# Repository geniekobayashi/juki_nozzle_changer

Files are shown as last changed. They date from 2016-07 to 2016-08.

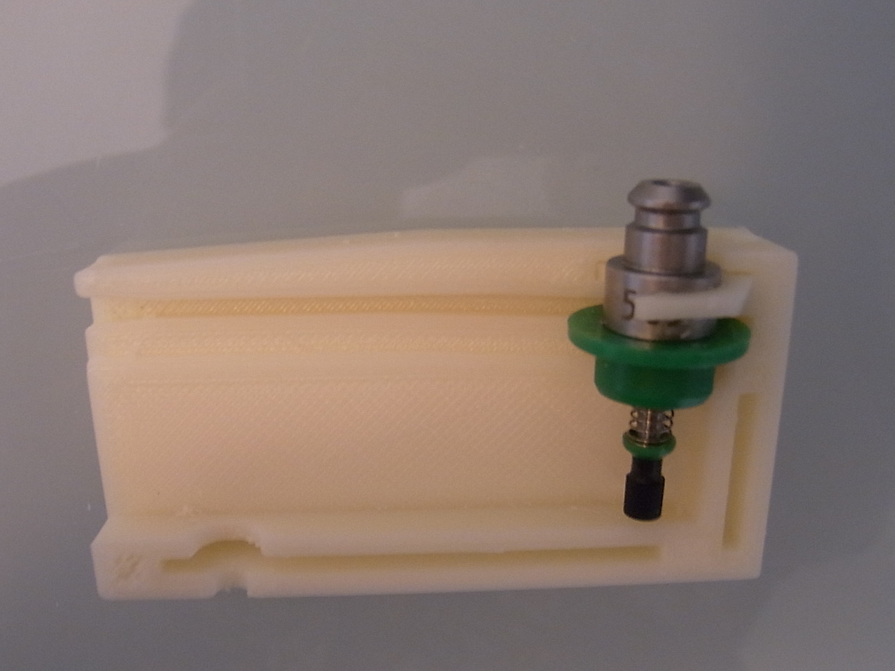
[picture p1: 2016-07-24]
images/RIMG0559.JPG

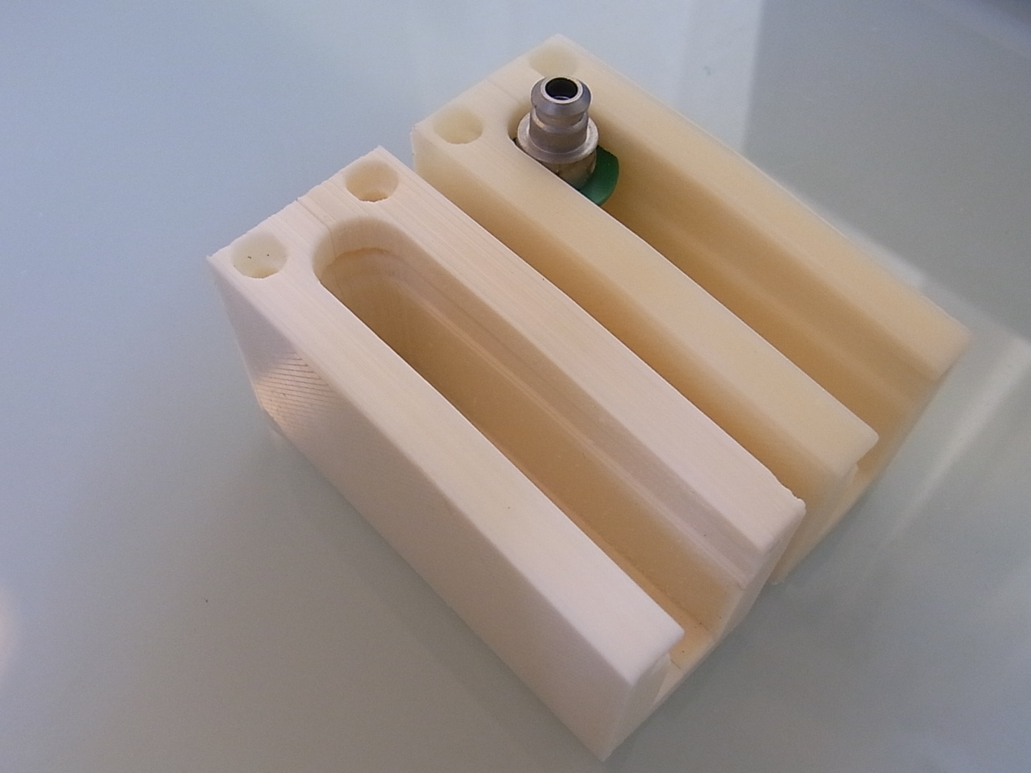
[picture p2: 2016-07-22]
images/RIMG0556.JPG

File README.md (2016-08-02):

## JUKI 50x nozzle changer using wtih Ray's holder.

Revision 0.1

It's a 3D printable automatic changer for JUKI 50x nozzle using wtih Ray Kholodovsky's custom made holder in OpenPnP project.

http://openpnp.org/

Assembly:

Please use a wide and flat sanding file for better adhering parts together, also use thin fine sanding files to make top surface and sliding ramp path smooth. Teflon spray coating is strongly recommended for silky smooth action and prolong the life of there parts. You may need a good plastic adhesive cement for final assembly. But, take care of clip when apply adhesive cement around - it should move freely.

Ganged mount plate can be modified to increase as much changer units as required by editing 'gang' parameter in "ganged_mount_plate.scad". Use M3 cap head hex screw L35mm x2 and L10mm x1 to fix each changer unit on this plate after M3 screw tapping. To fix the plate, use M4 pan-head screws.

Nozzle holding sequence:

 1. Holder moves down at the nozzle locating home position while outer ring sleeve moves toward upside enough.
 2. Holder slides horizontally toward ramp opening and leaves home with the nozzle dragging together.
 3. Nozzle moves upward a little bit (1mm) in the sequence at above and connects with the holder.
 4. Next, outher ring sleeve moves downward (2mm) and expand spring fully (at the top surface down slope part).
 5. Nozzle leaves from the changer and holding process is done.

Inspired by 'Pick-and-place automatic nozzle changer' - Karl Ekdahl. https://vimeo.com/144454866

Big thanks to Ray Kholodovsky!

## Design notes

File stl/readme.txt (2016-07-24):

These STL data are created for FDM 0.4mm nozzle printer. Do not need support materials on printing.

Revison 0.1: Use ABS for clip print out. Fine mode recommended to print these parts.

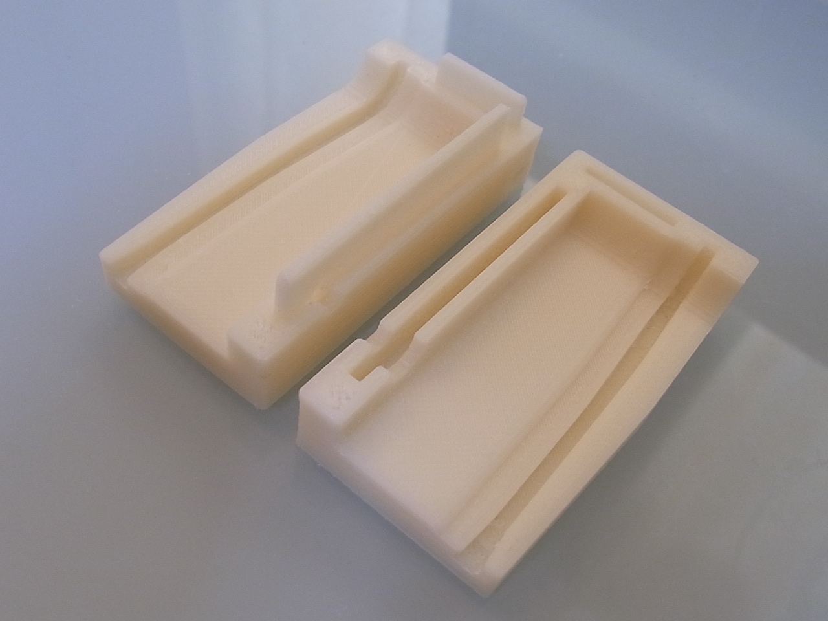
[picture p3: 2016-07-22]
images/RIMG0555.JPG

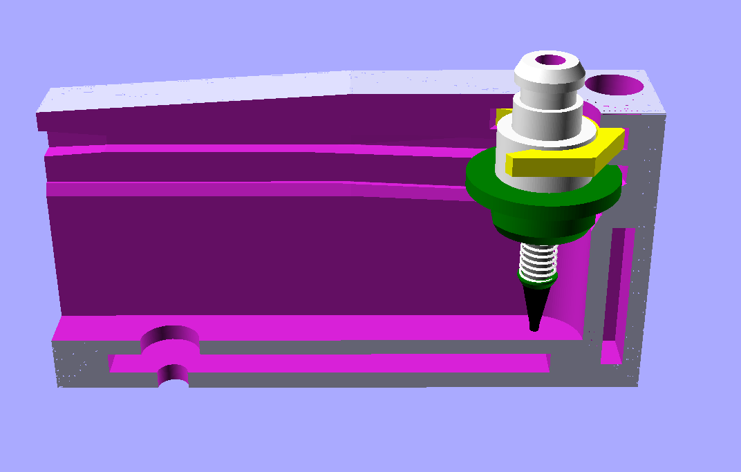
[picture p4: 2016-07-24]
images/OpenSCAD_image.png

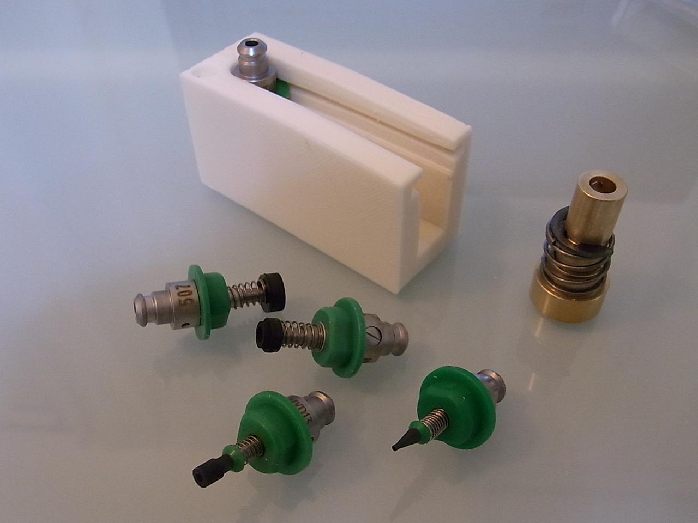
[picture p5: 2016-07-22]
images/RIMG0552.JPG

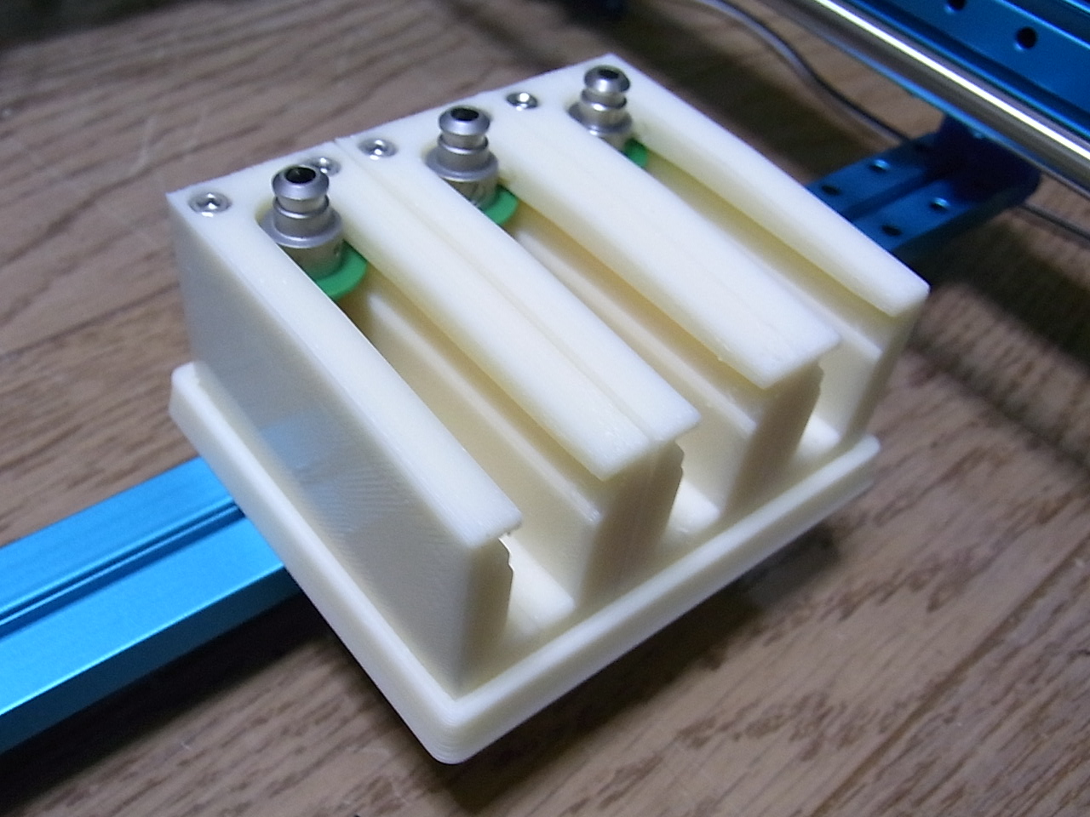
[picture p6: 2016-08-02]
images/RIMG0570.JPG

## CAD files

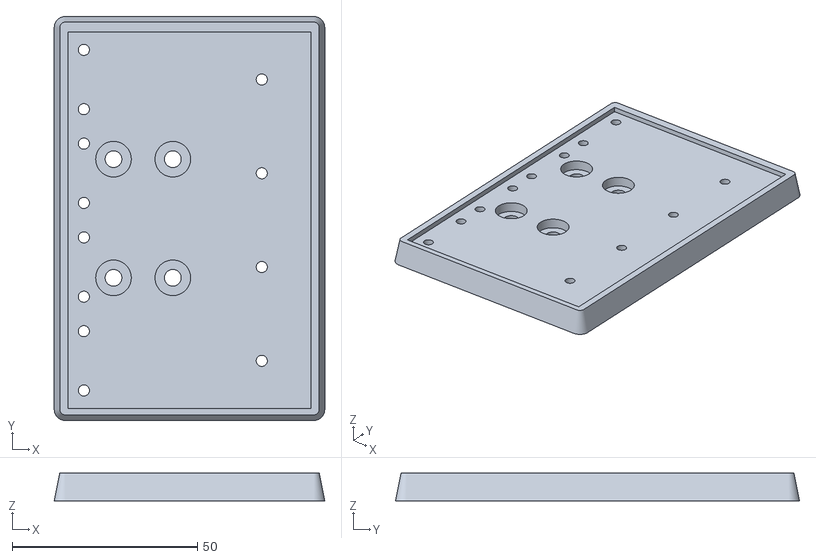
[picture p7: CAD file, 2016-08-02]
stl/ganged_mount_plate_4.stl
73.0 x 109.0 x 7.50

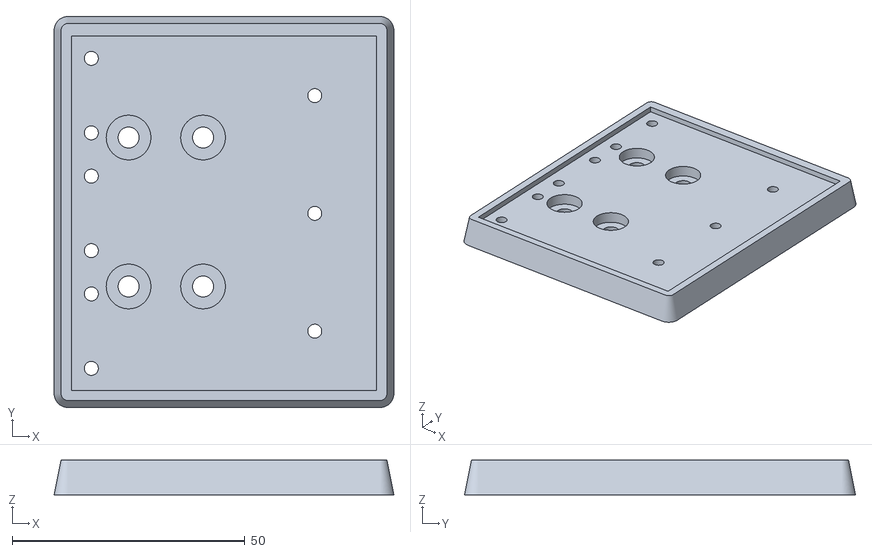
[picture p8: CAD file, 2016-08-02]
stl/ganged_mount_plate_3.stl
73.0 x 84.0 x 7.50

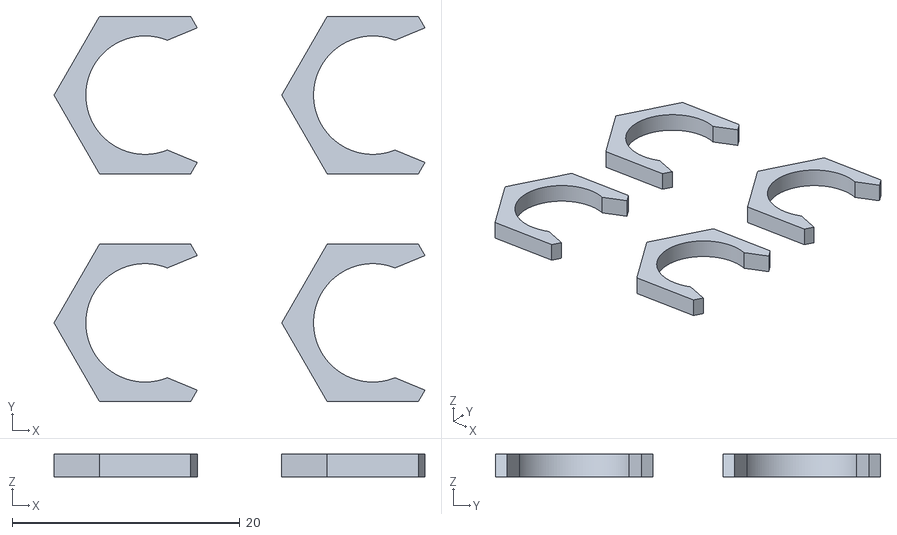
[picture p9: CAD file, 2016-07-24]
stl/clip_4.stl
32.6 x 33.9 x 2.00

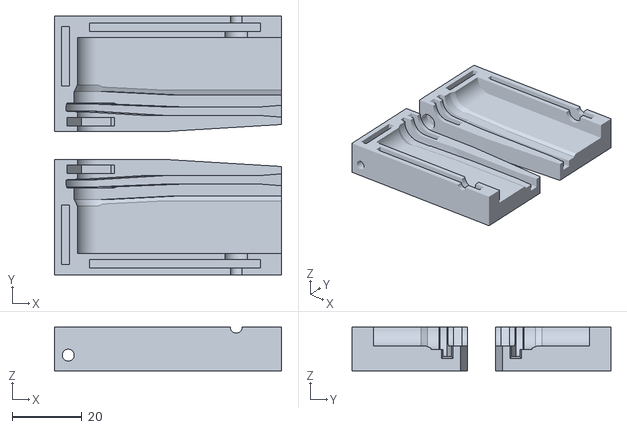
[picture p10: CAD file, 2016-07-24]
stl/nozzle_changer.stl
65.0 x 74.0 x 12.5

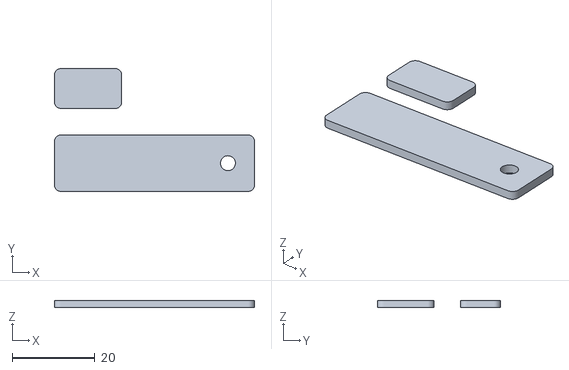
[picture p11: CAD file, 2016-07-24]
stl/nozzle_changer_joints.stl
48.2 x 29.6 x 1.80

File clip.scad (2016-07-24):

// Clip parts for nozzle changer
// by Genie Kibayashi, July 2016

$fn=128;
r_margin = 0.4;

//T2
module clip(){
difference(){
cylinder(h=2, r=8, $fn=6);

translate([0,0,-1])
cylinder(h=4, r=10/2+r_margin/2);

translate([4.8,0,-1])
cylinder(h=4, r=6, $fn=8);
 }
}

for (i = [0:20:20]) 
 for (j = [0:20:20]) {
translate([i,j,0])
clip();
}

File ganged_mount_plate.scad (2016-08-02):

// JUKI 50x nozzle changer w/Ray's holder
// ganged unit mount plate
// by Genie Kobayashi, July 2016
//
// OpenPnP project - http://openpnp.org/

$fn=128;

gang = 3; // 2 or more changer units

margin = 0.3; // 3D printer nozzle dia.
thickness = 25/2+margin; // changer half body

M3 = 3.0/2; // M3 screw tap hole - M3 socket cap hex screw x 3 @ each

// base plate fixing holes
M4 = 4.5/2;
offset = 8; // 16 to move near center - M4 pan-head screw x 4


module nozzle_changer_half(){

// body
rotate([90,0,0]) translate([-12,-30,0])
linear_extrude(height = thickness, convexity = 5) // base
	polygon(points = [ [0-margin, -3],[0-margin, 30],[32, 30],[65+margin, 28],
	[65+margin, -3],
]);

//M3
translate([-8,-8,-45])  cylinder(h=40, r=M3);
//translate([-8,-8,-3.5])  cylinder(h=10, r=6.2/2);

translate([30+10,0,-45])  cylinder(h=30, r=M3);
//translate([30+10,0,-27.6-1])  cylinder(h=5, r=6.5/2);
}

module nozzle_changer(){

nozzle_changer_half();

mirror([0,1,0])
nozzle_changer_half();
}


difference(){
// outline
hull(){
translate([-13,-gang*(thickness-margin)-1.5,-39])
cylinder(h=7.5,r1=3,r2=1.5);

translate([54,-gang*(thickness-margin)-1.5,-39])
cylinder(h=7.5,r1=3,r2=1.5);

translate([-13,gang*(thickness-margin)+1.5,-39])
cylinder(h=7.5,r1=3,r2=1.5);

translate([54,gang*(thickness-margin)+1.5,-39])
cylinder(h=7.5,r1=3,r2=1.5);
  }

for (i = [0:2*thickness-margin:(gang-1)*2*thickness]) {
 translate([0,-(gang-1)*thickness+i,0])
 nozzle_changer();
 }

// M4 fixing holes
translate([-8+offset,-16,-40])
cylinder(h=9,r=M4);

translate([8+offset,-16,-40])
cylinder(h=9,r=M4);

translate([-8+offset,16,-40])
cylinder(h=9,r=M4);

translate([8+offset,16,-40])
cylinder(h=9,r=M4);

// M4 head sink
translate([-8+offset,-16,-36])
cylinder(h=3,r=9.6/2);

translate([8+offset,-16,-36])
cylinder(h=3,r=9.6/2);

translate([-8+offset,16,-36])
cylinder(h=3,r=9.6/2);

translate([8+offset,16,-36])
cylinder(h=3,r=9.6/2);
}

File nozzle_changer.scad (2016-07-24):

// JUKI 50x nozzle changer w/Ray's holder
// by Genie Kobayashi, July 2016
//
// Reference to https://vimeo.com/144454866
// Pick-and-place automatic nozzle changer
// designed by Karl Ekdahl.
//
// Thanks to Ray Kholodovsky.
//
// OpenPnP project - http://openpnp.org/

$fn=128;

slide = 55;
thickness = 25/2;

r_margin = 0.4; // 3D printer nozzle dia.
h_margin = r_margin *2;

stop_dent = 0.5;

M3 = 3.4;

 module nozzle_movement(){

hull(){
     translate([0,0,-26.9+0.1]) cylinder(h=16, r=10/2+r_margin);
     translate([slide,0,-26.9+0.1]) cylinder(h=16, r=10/2+r_margin);
}
//         color("green")
hull(){
     translate([0,0,-11.4-1-h_margin/2]) cylinder(h=1.3+h_margin, r1=10/2+r_margin, r2=12/2+r_margin);
     translate([20,0,-11.4-h_margin/2]) cylinder(h=1.3+h_margin, r1=10/2+r_margin, r2=12/2+r_margin);
}
hull(){
     translate([20,0,-11.4-h_margin/2]) cylinder(h=1.3+h_margin, r1=10/2+r_margin, r2=12/2+r_margin);
     translate([slide,0,-11.4-h_margin/2]) cylinder(h=1.3+h_margin, r1=10/2+r_margin, r2=12/2+r_margin);
}
//         color("green")
hull(){
     translate([0,0,-10.1-1-h_margin/2]) cylinder(h=3.5+h_margin, r=12/2+r_margin);
     translate([20,0,-10.1-h_margin/2]) cylinder(h=3.5+h_margin, r=12/2+r_margin);
}
hull(){
     translate([20,0,-10.1-h_margin/2]) cylinder(h=3.5+h_margin, r=12/2+r_margin);
     translate([slide,0,-10.1-h_margin/2]) cylinder(h=3.5+h_margin, r=12/2+r_margin);
}
//     color("green")
hull(){
     translate([0,0,-6.6-1-h_margin/4]) cylinder(h=1.6+h_margin/2, r1=16.3/2+r_margin, r2=16.5/2+r_margin);
     translate([20,0,-6.6-h_margin/2]) cylinder(h=1.6+h_margin, r=16/2+r_margin);
}
hull(){
     translate([20,0,-6.6-h_margin/2]) cylinder(h=1.6+h_margin, r=16/2+r_margin);
     translate([slide,0,-6.6-h_margin/2]) cylinder(h=1.6+h_margin, r=16/2+r_margin);
}
 
hull(){
     translate([0,0,-5-1-h_margin/2]) cylinder(h=15+h_margin, r=10/2+r_margin);
     translate([20,0,-5-h_margin/2]) cylinder(h=15+h_margin, r=10/2+r_margin);
}
hull(){
     translate([20,0,-5-h_margin/2]) cylinder(h=15+h_margin, r=10/2+r_margin);
     translate([slide,0,-5-h_margin/2]) cylinder(h=15+h_margin, r=10/2+r_margin);
 }
}

module nozzle_changer_part(){
union(){
difference(){
// body
rotate([90,0,0]) translate([-12,-30,0])
linear_extrude(height = thickness, convexity = 5) // base
	polygon(points = [ [0, -3],[0, 30],[32, 30],[65, 28],
	[65, -3],
]);

nozzle_movement();

// home dent
//      translate([0,0,-5-1-h_margin/2]) cylinder(h=15+h_margin, r=10.5/2+r_margin);
//     translate([0,0,-6.6-1-h_margin/2]) cylinder(h=1, r=16.5/2+r_margin);
     translate([0,0,-6.6-1.1-h_margin/2]) cylinder(h=0.3, r1=16.5/2, r2=16.5/2+r_margin);
     translate([0,0,-11.4-1.5-h_margin/2]) cylinder(h=1.3+h_margin, r1=10/2+r_margin, r2=12/2+r_margin);

// mouth
hull(){
     translate([slide-8,0,-6.6-h_margin/2+1.2]) cube([1,16+2*r_margin,1.6+h_margin],center=true);
     translate([slide-1.5,0,-6.6-h_margin/2+1.2]) cube([1,17+2*r_margin,2.6+h_margin],center=true);
}

// grooves for joints
translate([-2,-7,-30-1])
cube([49,10,2+r_margin]); // T2

translate([-10,-5,-30])
cube([2+r_margin,10,17]); // T2

//M3
translate([-8,-8,-35])  cylinder(h=40, r=M3/2);
translate([-8,-8,-3.5])  cylinder(h=10, r=6.2/2);

translate([30+10,0,-35])  cylinder(h=10, r=M3/2);
translate([30+10,0,-27.6-1])  cylinder(h=5, r=6.5/2);

// clip
translate([0,0,-4])
cylinder(h=2+r_margin, r=8+r_margin, $fn=6);
  }
 }
}

rotate([90,0,0])
nozzle_changer_part();

mirror([0,0,1]) translate([0,-8,0]) rotate([270,0,0])
nozzle_changer_part();

//include <juki_nozzle.scad>
//translate([0,-9,0]) rotate([-90,0,0])
//nozzle();

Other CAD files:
nozzle_changer_joints.scad

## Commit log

2016-07-22 OpenPnP project
    [nozzle_changer.scad, nozzle_changer_L.stl, nozzle_changer_R.stl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]
2016-07-24 Clip embeded
    Revision 0.1
    [clip_4.stl, nozzle_changer.stl, nozzle_changer_joints.stl]
2016-08-02 ganged mount plate
